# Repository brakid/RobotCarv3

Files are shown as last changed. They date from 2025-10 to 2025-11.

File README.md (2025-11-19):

# Robot Car v3

## Objectives:
### P0: no obstacles
* robot car can drive towards a static target ✅
* robot car can follow a moving target ✅

Goal achieved using [Mobile Net SSD](https://github.com/chuanqi305/MobileNet-SSD) for person detection, the robot can follow an object, assuming there are not obstacles in the way. 

The robot uses a multi-threaded approach for: image capturing & person detection, sending control commands to the motors for setting the driving direction.

Using Mobile Net SSD instead of [Yolo v12n](https://docs.ultralytics.com/models/yolo12/) the latency to detect a person dropped from 0.35 sec to 0.095 sec (-73% detection latency) on a [Raspberry Pi 5 - 8GB](https://www.raspberrypi.com/products/raspberry-pi-5/) allowing for ~10 FPS.
### P1: obstacles
* robot car can drive towards a static target *redirecting when bumping into obstacles*
* robot car can follow a moving target *redirecting when bumping into obstacles*
### P2: obstacle avoidance
* robot car can drive towards a static target *avoiding obstacles*
* robot car can follow a moving target *avoiding obstacles*

## Robot Design
### P0:
* [Vacuum Robot inspired design](https://cookierobotics.com/056/): circular body-shape, 2 main wheels, caster wheel in the back
* camera mount (looking to the front)
* battery holders for 9V battery (and powerbank)
### P1:
* front: button bar to detect contact - 3 separate buttons: half-left, front, half-right
* expand adding Sonic Senor & Compass for Self-Localization
### P2:
* laser distance sensors for more accurate detection of obstacles in front & self-localization

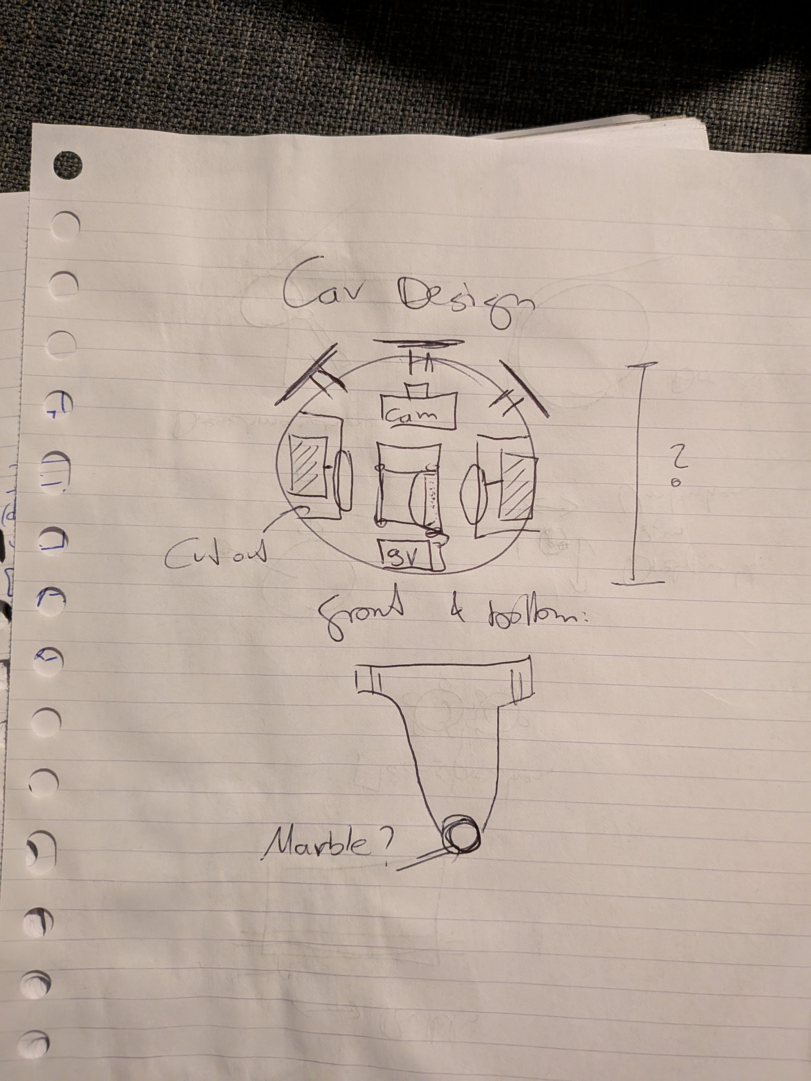
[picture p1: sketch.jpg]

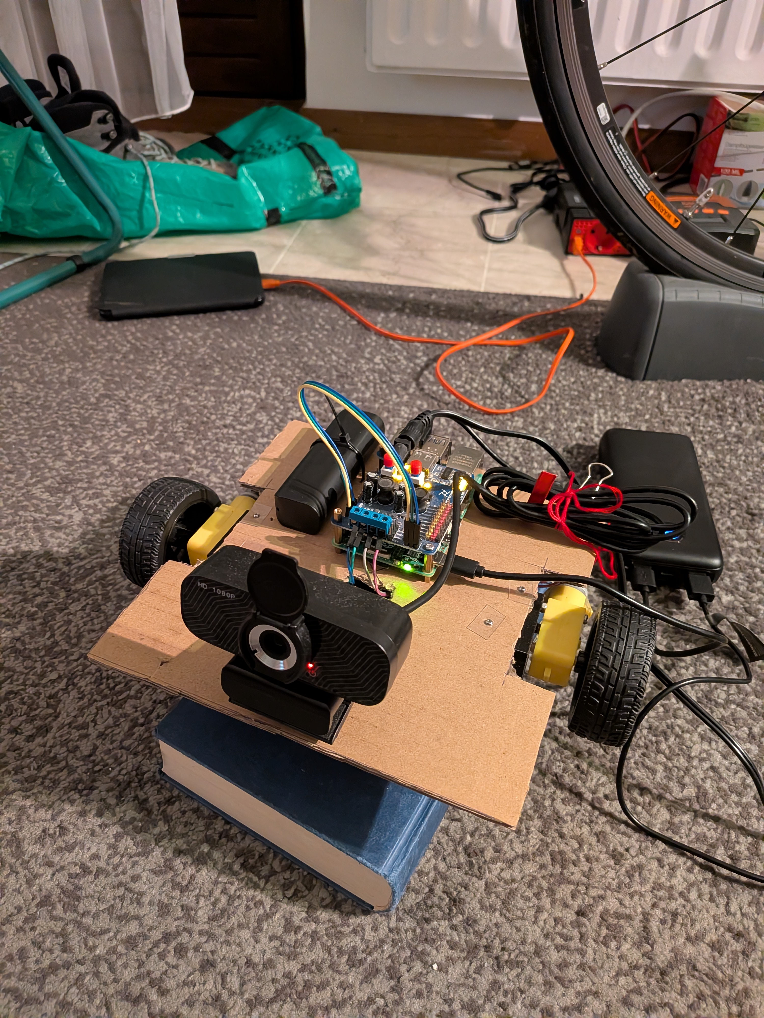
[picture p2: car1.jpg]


## Self-Driving capabilities
### P0:
* drive towards a defined object - object detection - correct steering to keep object in center (single object)
* adjust directions for moving targets
### P1:
* when detecting an obstacle (bumping into - detect obstacle direction with 3 button setup) - drive around (pre-programmed manoeuvers)
### P2:
* drive to defined position, obstacle avoidance (using sensors)
* path finding - drive towards object but account for obstacles
* internal mapping - given a room map (and the current position) - drive towards a position

## Design & Building
* wheel holders
* space for boards (Raspberry Pi & controller shield) - buy screws?
* cardboard model first?

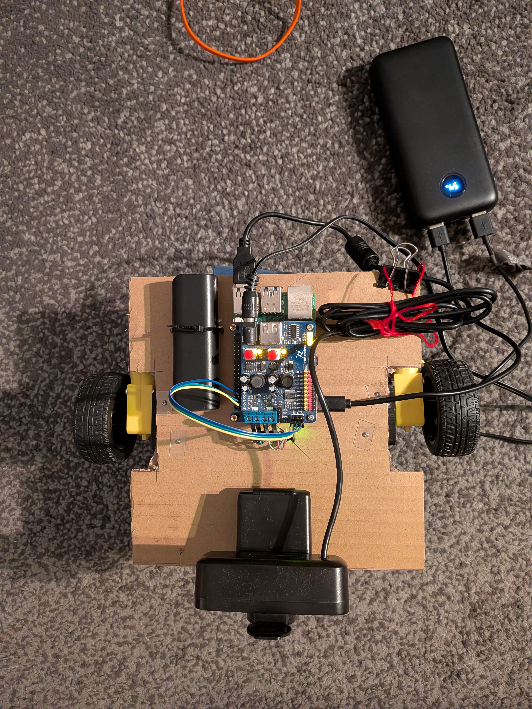
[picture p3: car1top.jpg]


## Distance sensing using ultra-sonic sound
* sweep the positions ahead (-15° - +15° (0° = straight ahead))
* measure the distance
* stop the car if any object ahead is getting too close ("emergency stop")
* use the detected object shapes to decide how to navigate across them (is an object on the right side -> derive around on the left - path-finding algorithm)

### Issues:
* ultra-sonic sound distances can fluctuate & are propne for polished object surfaces (*average over multiple sensor reads*)
* the sensor ([HC-SR04](https://howtomechatronics.com/tutorials/arduino/ultrasonic-sensor-hc-sr04/#hc-sr04-hardware-overview)) itself has a 15° measuring angle, meaning the object boundaries are fuzzy

#### Solution attempts
* as each reading covers a ~15° range, collect all overlapping readings per position, get the average in case the different readings overlap (variance < 0.3) -> sharper object edge detection

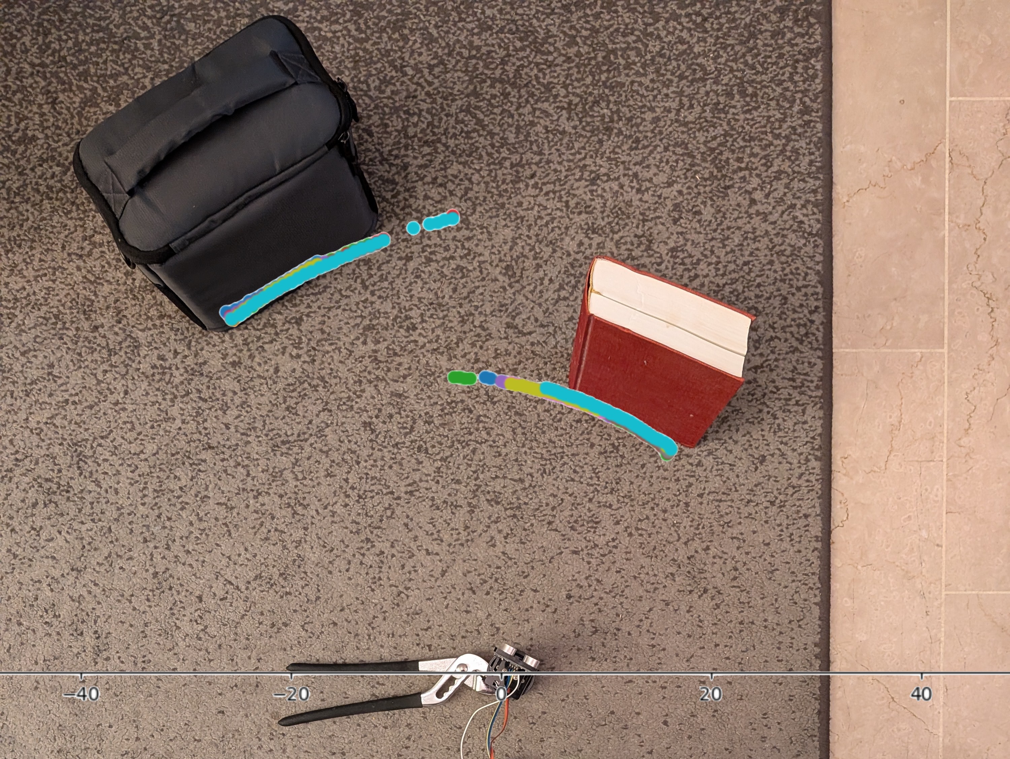
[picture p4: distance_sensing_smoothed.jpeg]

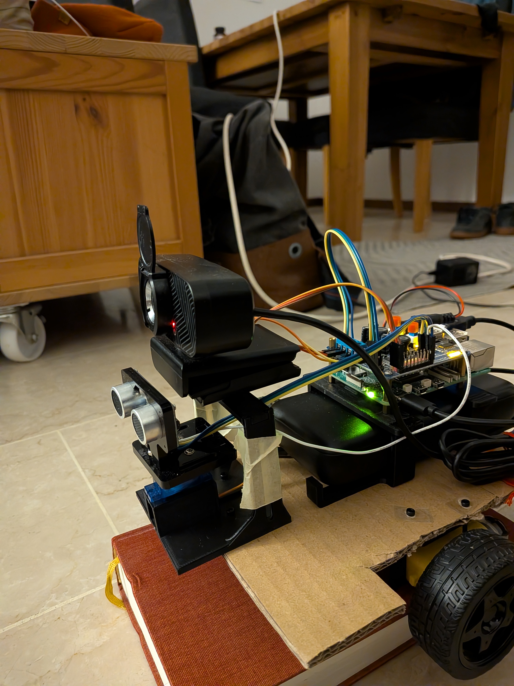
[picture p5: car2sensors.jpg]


## Steering
Idea:
* get current heading
* set target heading (based on desired offset)
 * register in compass (with degree of error)
* start motion, callback to stop
* compass triggers callback once reaching the desired position
 * stop motors

Implementation:
* compass: separate thread
 * API: standard granularity (5°?), register callback: target heading, function, once / repeatedly
 * store headings & callbacks, every loop (200 readings / second -> 0.005 wait time) delay -> check headings & whether to trigger some callback
  * store callbacks in Hashmap & read current [head - granularity / 2, head + granularity / 2] -> for each retrieved heading, callback pair -> call callback
* trigger x° degree in motor controller -> requests current heading, set callback in compass to stop motion
 * ensure compass reading happen fast enough, or cause callback also to fire if position goes beyond the planned value (e.g target 90°, moving clockwise -> an< heading >= 90° triggers the stop)

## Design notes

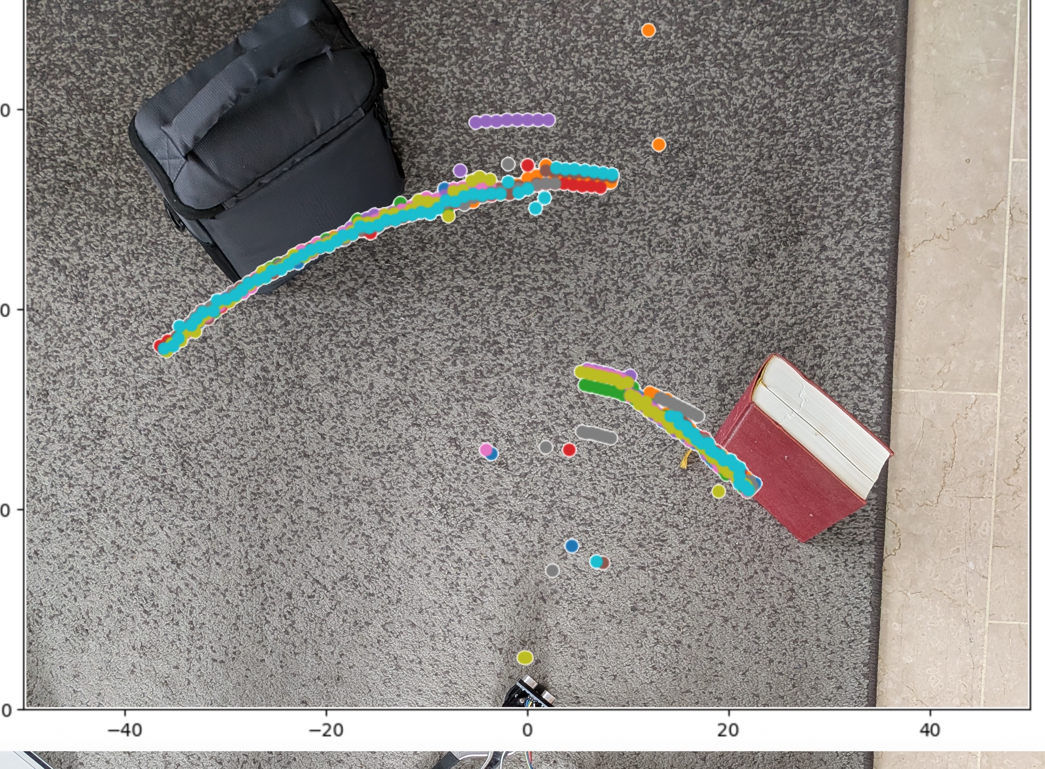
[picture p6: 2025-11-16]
distance_sensor.jpg

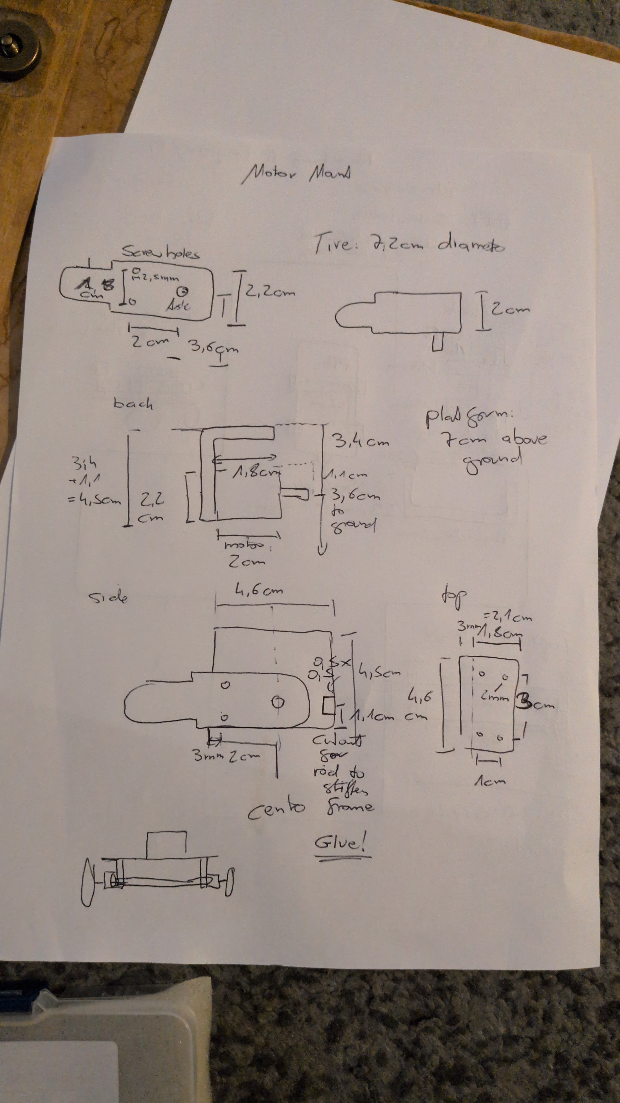
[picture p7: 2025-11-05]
drawings/motor_mount.jpeg

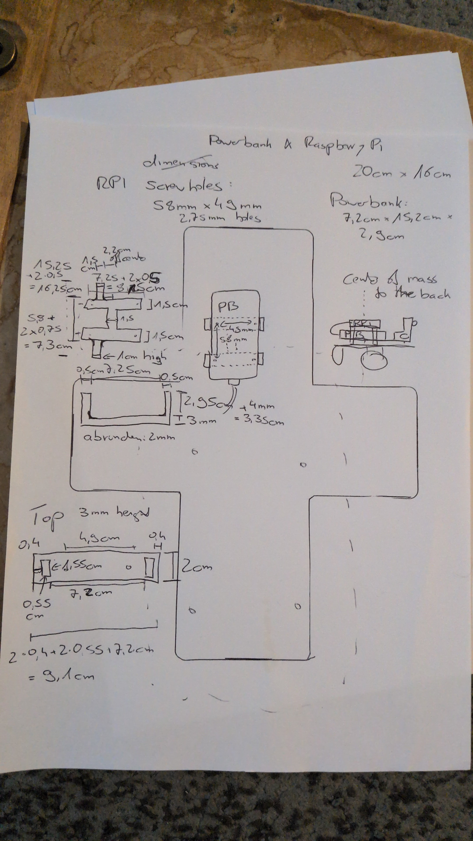
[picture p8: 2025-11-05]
drawings/powerbankrpi_mount.jpeg

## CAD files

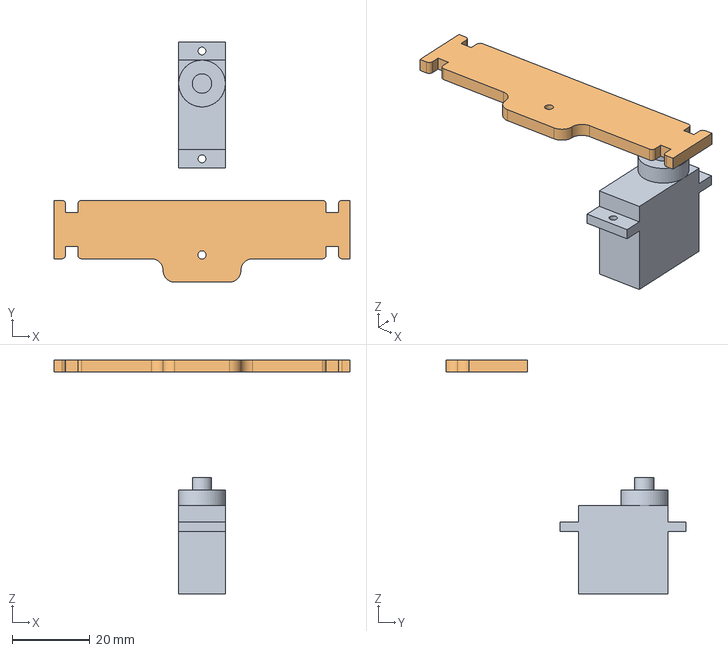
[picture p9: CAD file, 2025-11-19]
drawings/SensorMount.FCStd
76.0 x 61.7 x 60.0 mm
Servo
Top

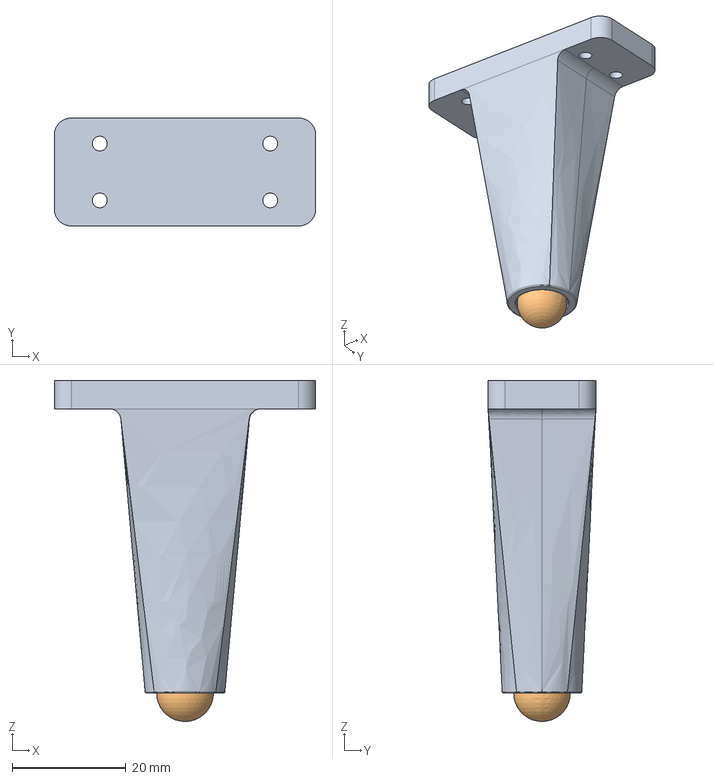
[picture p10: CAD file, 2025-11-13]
drawings/BallRoller-v1.FCStd
46.0 x 19.0 x 60.0 mm

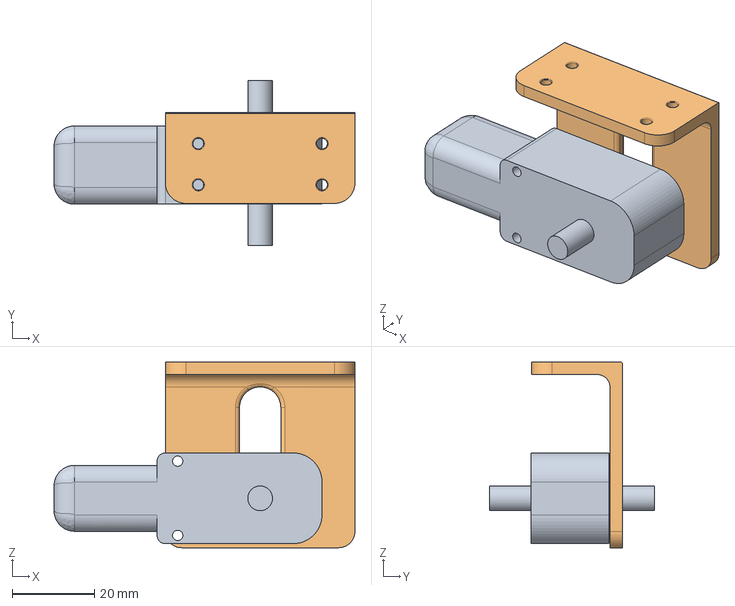
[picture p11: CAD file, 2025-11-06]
drawings/MotorMount-v1.FCStd
73.0 x 40.0 x 45.0 mm
Motor
MotorMount

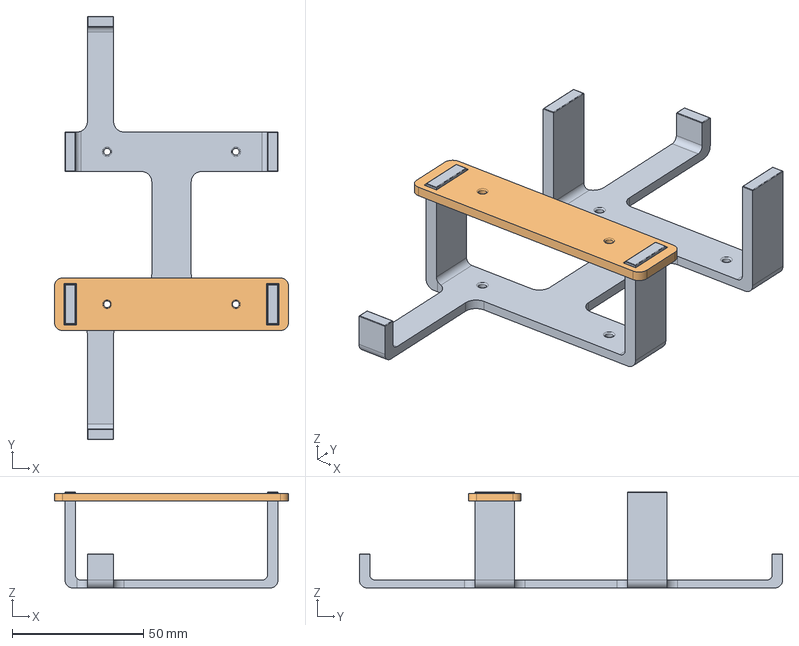
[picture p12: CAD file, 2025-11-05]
drawings/PowerbankRpiMount-v1.FCStd
89.0 x 161.0 x 36.5 mm
Bottom
Top

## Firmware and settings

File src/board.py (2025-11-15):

import smbus
import time
from threading import Lock

class Board:
    CMD_SERVO1 = 0
    CMD_PWM1 = 4
    CMD_PWM2 = 5
    CMD_DIR1 = 6
    CMD_DIR2 = 7
    CMD_SONIC = 12
    SONIC_MAX_HIGH_BYTE = 50
    SERVO_MAX_PULSE_WIDTH = 2500
    SERVO_MIN_PULSE_WIDTH = 500
    
    def __init__(self, addr=0x18):
        self.address = addr
        self.bus=smbus.SMBus(1)
        self.bus.open(1)
        self.mutex = Lock()

    def _write_registers(self, target: int, value: any):
        with self.mutex:
            value = int(value)
            data = [value>>8, value&0xff]
            try:
                self.bus.write_i2c_block_data(self.address, target, data)
                time.sleep(0.001)
                self.bus.write_i2c_block_data(self.address, target, data)
                time.sleep(0.001)
                self.bus.write_i2c_block_data(self.address, target, data)
                time.sleep(0.001)
            except Exception as e:
                print('I2C Error :', e)

    def _read_register(self, target: int) -> int:		
        with self.mutex:
            self.bus.write_byte(self.address, target)
            high_byte = self.bus.read_byte_data(self.address, target)
            
            self.bus.write_byte(self.address, target + 1)
            low_byte = self.bus.read_byte_data(self.address, target + 1)
            
            if(high_byte < self.SONIC_MAX_HIGH_BYTE):
                return high_byte << 8 | low_byte
            else:
                return 0

    def _convert_angle_to_servo_pwm(self, angle: float) -> int:
        return int((self.SERVO_MAX_PULSE_WIDTH - self.SERVO_MIN_PULSE_WIDTH) * angle / 180.0 + self.SERVO_MIN_PULSE_WIDTH)

    def stop(self):
        self._write_registers(self.CMD_DIR1, 1)
        self._write_registers(self.CMD_DIR2, 1)
        
        self._write_registers(self.CMD_PWM1, 0)
        self._write_registers(self.CMD_PWM2, 0)
    
    def forward(self, pwm: int = 500):
        self._write_registers(self.CMD_DIR1, 1)
        self._write_registers(self.CMD_DIR2, 1)

        self._write_registers(self.CMD_PWM1, 1000)
        self._write_registers(self.CMD_PWM2, 1000)
        self._write_registers(self.CMD_PWM1, pwm)
        self._write_registers(self.CMD_PWM2, pwm)

    def backward(self, pwm: int = 500):
        self._write_registers(self.CMD_DIR1, 0)
        self._write_registers(self.CMD_DIR2, 0)
        
        self._write_registers(self.CMD_PWM1, 1000)
        self._write_registers(self.CMD_PWM2, 1000)
        self._write_registers(self.CMD_PWM1, pwm)
        self._write_registers(self.CMD_PWM2, pwm)

    def turn_left(self, pwm: int = 500):
        self._write_registers(self.CMD_DIR1, 1)
        self._write_registers(self.CMD_DIR2, 0)
        
        self._write_registers(self.CMD_PWM1, 1000)
        self._write_registers(self.CMD_PWM2, 1000)
        self._write_registers(self.CMD_PWM1, pwm)
        self._write_registers(self.CMD_PWM2, pwm)
    
    def turn_right(self, pwm: int = 500):
        self._write_registers(self.CMD_DIR1, 0)
        self._write_registers(self.CMD_DIR2, 1)
        
        self._write_registers(self.CMD_PWM1, 1000)
        self._write_registers(self.CMD_PWM2, 1000)
        self._write_registers(self.CMD_PWM1, pwm)
        self._write_registers(self.CMD_PWM2, pwm)

    def set_servo_angle(self, servo: int, angle: float):
        self._write_registers(servo, self._convert_angle_to_servo_pwm(angle))

    def get_sonic_distance(self):
        sonic_time = self._read_register(self.CMD_SONIC)
        distance = sonic_time * 0.5 * 343.0 / 10000.0
        return distance

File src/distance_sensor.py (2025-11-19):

import logging
from board import Board
import time
from typing import Callable, Optional
from timer import timer
import numpy as np
from collections import defaultdict
from threading import Thread, Lock

'''
# simple logic
def get_distance_ahead(reverse: bool = False, min_angle: float = 45, max_angle: float = 135, lower_threshold: float = 5, upper_threshold: float = 70) -> np.array:
    distances= []
    angle_range = range(min_angle, max_angle + 1, 1) if not reverse else range(max_angle, min_angle - 1, -1)
    for angle in angle_range:
        board.set_servo_angle(board.CMD_SERVO1, angle)
        distance = get_distance()
        if (distance > lower_threshold and distance < upper_threshold):
            distances.append((angle, distance))
    coordinates = np.array([ [ np.cos(np.radians(angle)) * distance, np.sin(np.radians(angle)) * distance ] for (angle, distance) in distances ])
    return coordinates
'''

class DistanceSensor:
    def __init__(self, board: Board, emergency_stop_distance_threshold: float, emergency_stop_callback: Callable[[], None]):
        self.logger = logging.getLogger('DistanceSensor')
        self.board = board
        self.servo = board.CMD_SERVO1

        # Thread control
        self.running = False
        self.thread = None
        self.distances: Optional[np.array] = None
        self.lock = Lock()
        self.emergency_stop_distance_threshold = emergency_stop_distance_threshold
        self.emergency_stop_callback = emergency_stop_callback


    def start(self):
        if not self.running:
            self.running = True
            self.thread = Thread(target=self._distance_loop, daemon=True)
            self.thread.start()
            logging.info('Distance sensor started')
    
    def stop(self):
        self.running = False
        if self.thread:
            self.thread.join()
        logging.info('Distance sensor stopped')

    def _get_distance(self, attempts: int = 2) -> float:
        sum = 0.0
        for _ in range(attempts):
            sum += self.board.get_sonic_distance()
            time.sleep(0.005) # enough time to have sound pass ~1.7m
        return sum / attempts

    @timer
    def _get_distance_ahead_smoothed(self, reverse: bool = False, min_angle: float = 75, max_angle: float = 105, lower_threshold: float = 5, upper_threshold: float = 70, variance_threshold: float = 0.3, measuring_range: int = 7) -> np.array:
        distances = defaultdict(list)
        angle_range = range(min_angle, max_angle + 1, 1) if not reverse else range(max_angle, min_angle - 1, -1)
        for angle in angle_range:
            self.board.set_servo_angle(self.board.CMD_SERVO1, angle)
            distance = self._get_distance()
            if (distance >= lower_threshold and distance <= upper_threshold):
                for a in range(angle + (-1) * measuring_range, angle + measuring_range + 1):
                    distances[a].append(distance)
        smoothed_distances = [ (k, np.array(v).mean()) for k, v in distances.items() if np.array(v).var() < variance_threshold ]
        coordinates = np.array([ [ np.cos(np.radians(angle)) * distance, np.sin(np.radians(angle)) * distance ] for (angle, distance) in smoothed_distances ])
        return coordinates
    
    def _distance_loop(self):
        self.logger.info('Distance sensor loop started')

        is_reversed = False
        
        while self.running:
            distances = self._get_distance_ahead_smoothed(is_reversed)
            if len(distances.shape) == 2:
                with self.lock:
                    self.distances = distances
                is_reversed = not is_reversed
                
                if np.median(distances[:, 1]) < self.emergency_stop_distance_threshold:
                    self.emergency_stop_callback()
        
        self.logger.info('Distance sensor loop started')

    def get_distances(self) -> Optional[np.array]:
        with self.lock:
            try:
                return self.distances
            finally:
                self.distances = None

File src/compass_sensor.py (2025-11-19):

from compass import Compass
import logging
import time
from typing import Optional
from timer import timer
import numpy as np
from collections import defaultdict
from threading import Thread, Lock

class CompassSensor:
    def __init__(self, compass: Compass):
        self.logger = logging.getLogger('CompassSensor')
        self.compass = compass

        # Thread control
        self.running = False
        self.thread = None
        self.heading: Optional[float] = None
        self.lock = Lock()

    def start(self):
        if not self.running:
            self.running = True
            self.thread = Thread(target=self._compass_loop, daemon=True)
            self.thread.start()
            logging.info('Compass sensor started')
    
    def stop(self):
        self.running = False
        if self.thread:
            self.thread.join()
        logging.info('Compass sensor stopped')

    #@timer
    def _get_heading(self, attempts: int = 5) -> float:
        sum = 0.0
        for _ in range(attempts):
            sum += self.compass.get_heading()
            time.sleep(0.005) # 200 HZ compass
        return sum / attempts
    
    def _compass_loop(self):
        self.logger.info('Compass sensor loop started')
        
        while self.running:
            with self.lock:
                self.heading = self._get_heading()
                
        self.logger.info('Compass sensor loop stopped')

    def get_heading(self) -> Optional[float]:
        with self.lock:
            try:
                return self.heading
            finally:
                self.heading = None

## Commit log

2025-11-05 Drawings Powerbank Mount
    [PowerbankRpiMount-v1.FCStd]
2025-11-06 Adding motor mount sketch
    [MotorMount-v1.FCStd]
2025-11-09 Ball roller for robot back
    [BallRoller-v1.FCStd]
2025-11-13 First following robot version
    Can track a human, steers to focus on the human, decides turning angle based on position of the human
    [BallRoller-v1.FCStd]
2025-11-15 Adding distance sensor mounted on a servo to measure distance ahead
2025-11-16 Smooting distance sensor readings
2025-11-17 Including distance sensor in driving
2025-11-19 Adding compass - next: add logic to turn by x degree
    [SensorMount.FCStd]
